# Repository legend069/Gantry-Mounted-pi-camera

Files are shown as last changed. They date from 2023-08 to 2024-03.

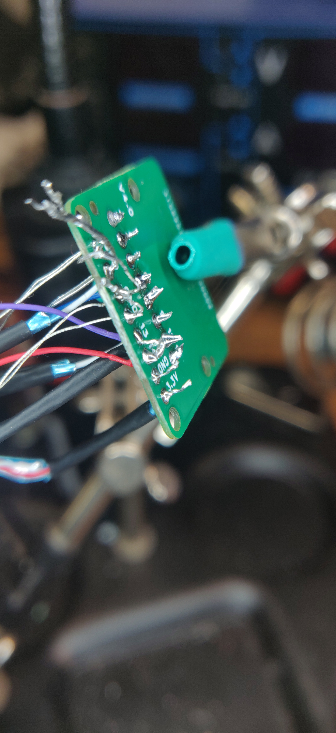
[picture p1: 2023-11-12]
Pictures/Build Process Pictures/IMG_20230614_181707.jpg

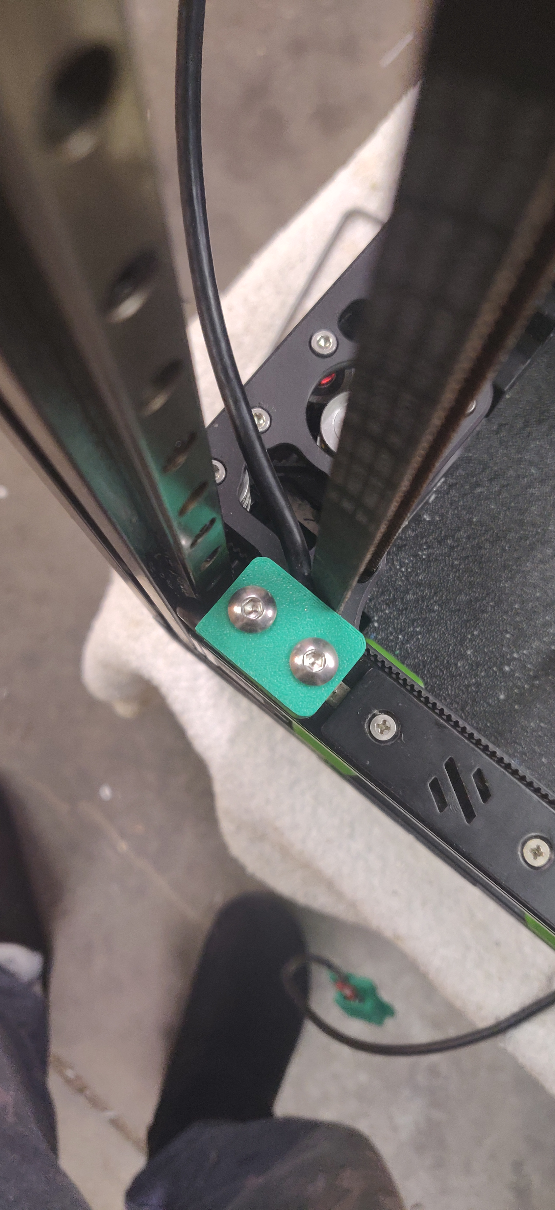
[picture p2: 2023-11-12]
Pictures/Build Process Pictures/IMG_20230511_184907.jpg

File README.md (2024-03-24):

# Gantry-Mounted-pi-camera
description - work in progress  

GPU-Z_GeZQuU00W8

# summary
there are two pi camera versions to choose from.
plug and play - exactly as it sounds. plug cable into PCB's and the FPC cables in and away you go!
  but this one costs more $$ in parts.

raw dog - i like to call it raw dog because you're basically raw dogging it.
  this one is for the soldering experts(or atleast above beginner) you cut up a DP cable(any length as long as it will reach point a to point b)
  strip the very tiny and fragile wires and solder them directly to the PCB.
  is a cheaper for parts. [tips](https://github.com/legend069/Gantry-Mounted-pi-camera/edit/main/README.md#tips-for-soldering-raw-dog)

  note: to help with raw-dog method, i've created a extra [PCB](https://github.com/legend069/Gantry-Mounted-pi-camera/tree/main/gerbers/ready%20to%20order%20files/raw_dog_full_display_port) using this PCB and the normal raw-dog one you only have to cut 1 end of the cable. but since the display port wires get switched inside the cable, you need to figure what end is what before you cut it.

i originally wanted this to be cheap, so i started off with cat5e networking cable. yes this does actually work but only over short distances.<1.5 meter

## whats the differences between the two?
*  plug-play takes up more Z height(this is mainly because of the cable)
*  raw-dog much more compact, but requires a skilled and patient soldering

  the max FPS you can get between the two is the same, the limiter is the camera, my target for the project was 30fps. during my testing phase it can push up to 45(pi camera v3 wide) before it starts to have frame stutter/visable noise.
  if you're going with the raw-dog method getting maxfps (40+) gets harder and harder with the soldering work. because you need to get all 8 wires to the PCB the **same length!**

## tips for soldering raw-dog
* this takes a long time, it'll take around 2 hours to solder both PCB's + add some more time if some wires break :angry: during the trials i broke around 10 wires during moving from the solder work bench to the printer.
* the pro tip i found that helped out a bunch was to use some cat5e(any solid core network cable) and extend the ends of the DisplayPort cable. and heatshrink the bits in between.[picture](https://github.com/legend069/Gantry-Mounted-pi-camera/blob/main/Pictures/Build%20Process%20Pictures/IMG_20230618_065408.png)
* as long as you **cut** the lengths as good as you can, then tin the wires and start soldering. use very light solder with the tinning and PCB work.
  because you can use tweezers and slightly pull/press on the wire to help get it aligned up with the other **this is a critical step!** [reference](https://github.com/legend069/Gantry-Mounted-pi-camera/blob/main/Pictures/Build%20Process%20Pictures/IMG_20230614_181707.jpg) the important wires that need to length match are the top 8 (pads 2-12) the others don't matter. and yes you do need to **solder all the shielded wires to GND** too.
* if you can't get the wires length matching as close as possible to perfect. don't worry, it's not the end of the world. you'll just get frame [stutter/visual noise](https://www.google.com.au/search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) on high framerates.

if you want more pictures they're [here](https://github.com/legend069/Gantry-Mounted-pi-camera/tree/main/Pictures)

the picture below is the raw-dog camera in action- pi camera V3 wide
snapshot

the picture below is the raw-dog camera in action- pi camera V2
snapshotV2cam

and this one is the micro-hdmi (plug and play) pi camera V2
micro1

i don't have the photo for the micro-hdmi (plug and play) pi camera V3 wide(since i didn't have the v3 camera at the time) 

# BOM (build of materials) 
below links is what i bought and are guarenteed to work. you're more than welcome to find others but they might not work.
* for rawdog  
  [FPC cable 50mm](https://au.mouser.com/ProductDetail/710-686715050001)  
  [raw-dog DP-DP cable 2m](https://cplonline.com.au/alogic-eldp-02-elements-2m-displayport-cable-ver-1-2-male-to-male.html) - PN alogic ELDP-02  
  M2 screws 12mm x4 & 16mm x4  

* plug and play(micro-hdmi)  
  [FPC cable 50mm](https://au.mouser.com/ProductDetail/710-686715050001)  
  [micro-hdmi to hdmi cable 2m](https://www.digikey.com.au/en/products/detail/tripp-lite/P570-006-MICRO/4438902)  
  [adapter](https://www.digikey.com.au/en/products/detail/seeed-technology-co-ltd/320210001/5487747)  
  M2 screws 12mm-14mm x4 & 20mm x4   

### alternates
[adapter alternate-UN TESTED](https://au.mouser.com/ProductDetail/Seeed-Studio/320210001?qs=SElPoaY2y5IpesjEUALrcQ%3D%3D)  
[cheaper option-UN TESTED](https://au.rs-online.com/web/p/raspberry-pi-cables/1871376)  
[FPC cable 50mm alternate](https://www.digikey.com.au/short/bmt4hz0f)  

# FAQ
* can i destroy my pi camera using this?  
  no, not unless you mess up the wiring with raw-dog method.
* do i have to use your repo?  
  no, you're more than welcome to use any other pi camera streaming software.
* do i need supports for the printable files?  
  for most of them yes, but use your 3d printing knowledge to determine if some areas are needed or not.
* will the cable that's inside the y extrusion wear out over time?  
  no, the cable i spefically looked for would fit nicely in the gaps and not have any clearance issues.
* do i need a second drag chain for this?  
  only if your current drag chain won't be able to fit the extra cable.
* will i lose any printable height in XYZ?  
  no, not for the raw-dog camera
  for the micro-hdmi version you shouldn't but then you have a different printer to me, so check the cad file 😄
* how much networking bandwidth does this use?  
  for the V3 camera -camera-width=2304 -camera-height=1296 at 30 fps it's around 50mbps while watching the stream.
  if you close the stream from your phone/pc tab the stream will end and stop using the network bandwidth.
* can i use this for timelapes?  
  you sure can! it's still your standard pi camera.

# sounds great! how i get one?
  order the parts from digikey/mouser
  [gerber files](https://github.com/legend069/Gantry-Mounted-pi-camera/tree/main/gerbers/ready%20to%20order%20files)
  steps for PCB ordering coming soon....

```diff
- note:PCB thickness must be 0.8mm!
```

## repo download
```
cd ~
git clone https://github.com/legend069/Gantry-Mounted-pi-camera.git
```
## install commands
```
sudo apt-get -y install libavformat-dev libavutil-dev libavcodec-dev libcamera-dev liblivemedia-dev v4l-utils pkg-config xxd build-essential
cd ~
ln -s /home/pi/Gantry-Mounted-pi-camera/repo/camera-streamer /home/pi/camera-streamer
cd camera-streamer/
make
sudo make install
```
## setup commands for camera
```
systemctl enable $PWD/service/camera-streamer-raspi-v2-8MP.service 
systemctl start camera-streamer-raspi-v2-8MP 
------or------ 
systemctl enable $PWD/service/camera-streamer-raspi-v3-12MP.service 
systemctl start camera-streamer-raspi-v3-12MP.service 
```
### to view logs
``journalctl -xef -u camera-streamer-raspi-v2-8MP ``

all the credit for the code goes to this guy https://github.com/ayufan/camera-streamer

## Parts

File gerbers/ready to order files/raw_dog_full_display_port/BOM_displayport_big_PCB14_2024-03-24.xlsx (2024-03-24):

No. | Quantity | Comment | Designator | Footprint | Value | Manufacturer Part | Manufacturer | Supplier Part | Supplier
1 | 1 | 3VD51203-3D6A-7H | CN2 | DP-SMD_3VD51203-3D6A-7H |  | 3VD51203-3D6A-7H | FOXCONN(富士康) | C2761456 | LCSC
2 | 1 | F1003WR-S-15PNLNG1GB0R | FPC2 | FPC-SMD_15P-P1.00_L5.5-W22.0 |  | F1003WR-S-15PNLNG1GB0R | HR(灿达) | C247796 | LCSC

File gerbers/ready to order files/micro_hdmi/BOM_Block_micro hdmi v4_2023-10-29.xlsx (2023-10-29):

No. | Quantity | Comment | Designator | Footprint | Value | Manufacturer Part | Manufacturer | Supplier Part | Supplier
1 | 1 | F1003WR-S-15PNLNG1GB0R | FPC1 | FPC-SMD_15P-P1.00_L5.5-W22.0 |  | F1003WR-S-15PNLNG1GB0R | HR(灿达) | C247796 | LCSC
2 | 1 | HDMI-101S | USB1 | HDMI-SMD_HDMI-101S |  | HDMI-101S | XUNPU(讯普) | C720620 | LCSC

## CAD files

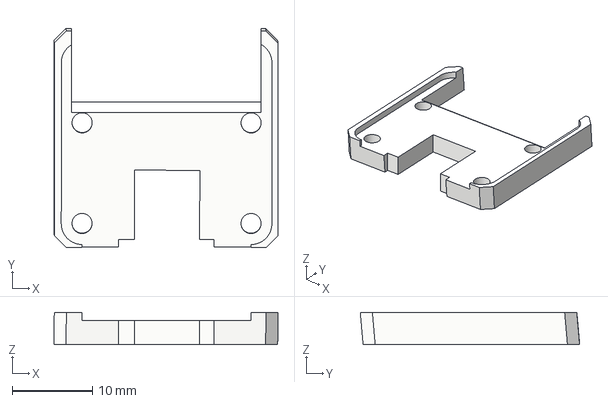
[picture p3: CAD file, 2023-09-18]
3mf printable files/micro-hdmi/first-prototype-mounting/microHDMI_mid2.3mf
27.8 x 27.3 x 4.00 mm

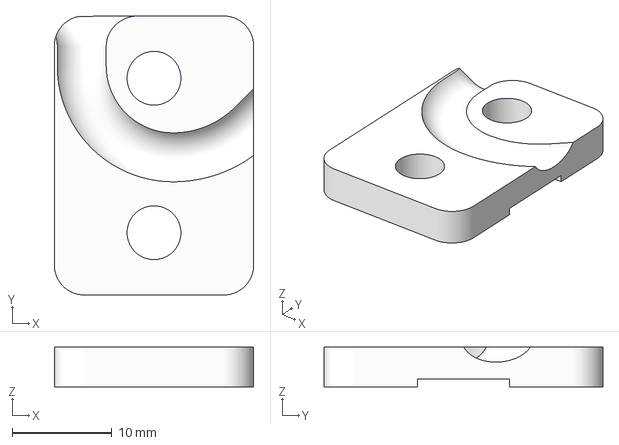
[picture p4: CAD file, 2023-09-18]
3mf printable files/motor-side-parts/motor_end_1.3mf
20.0 x 28.0 x 4.00 mm

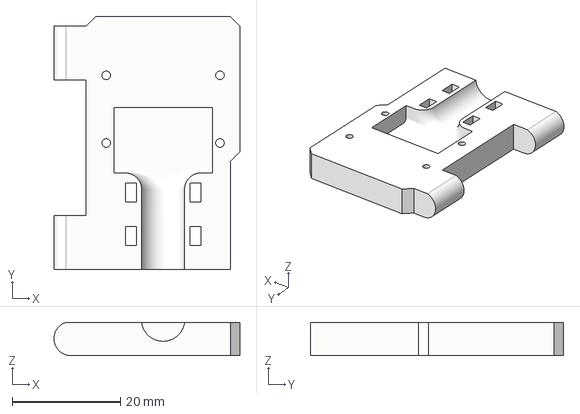
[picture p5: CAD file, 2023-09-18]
3mf printable files/pi-side-parts/RawDog_pi_end_2.3mf
34.3 x 46.8 x 6.15 mm

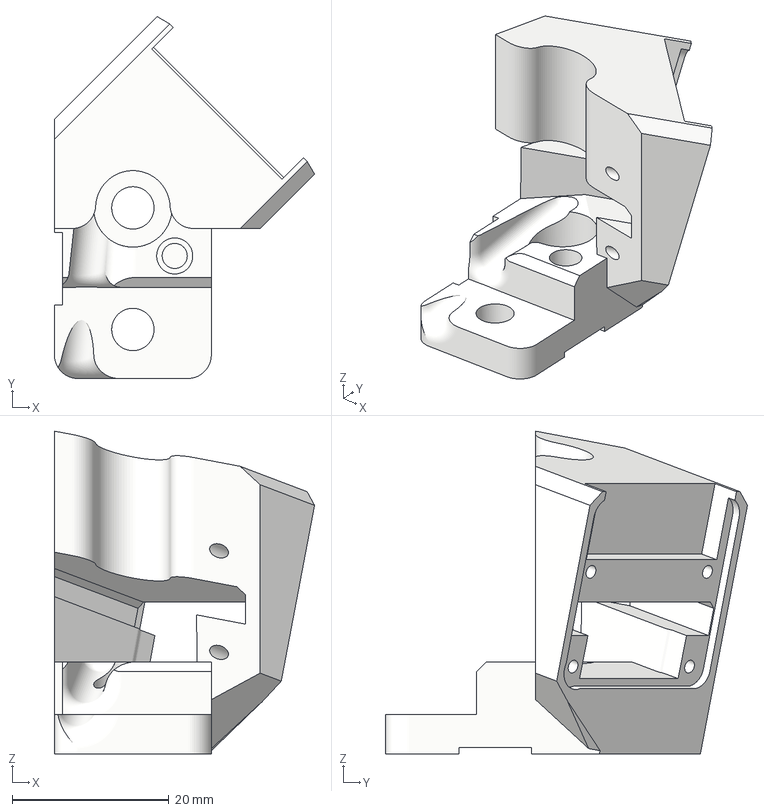
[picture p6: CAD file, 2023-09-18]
3mf printable files/raw-dogV2camera/first-prototype-mounting/RawDog_bottom_V3.3mf
33.2 x 46.1 x 41.1 mm

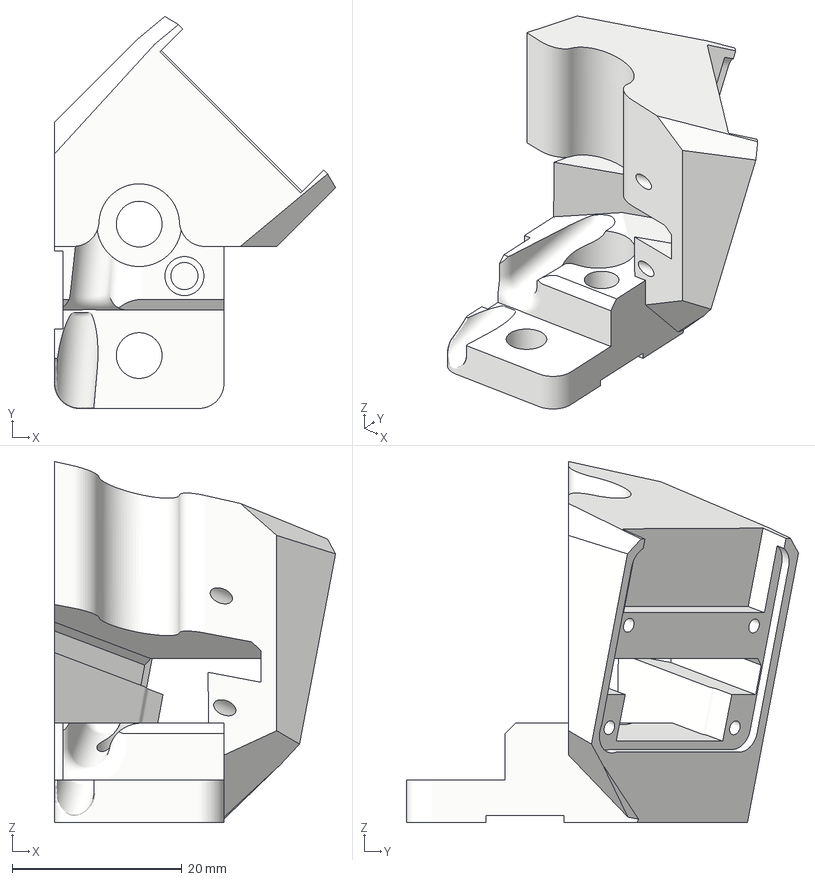
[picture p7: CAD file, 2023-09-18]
3mf printable files/raw-dogV3camera/first-prototype-mounting/RawDog_bottom_V3 (1).3mf
33.2 x 46.2 x 42.6 mm

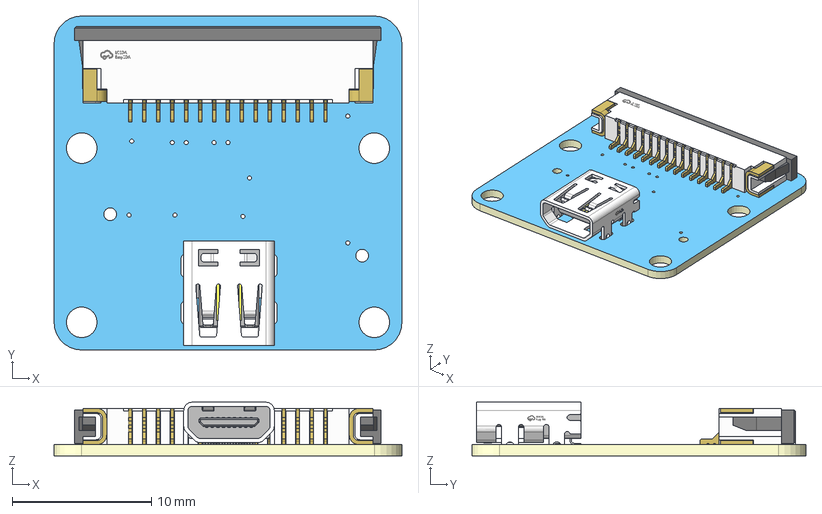
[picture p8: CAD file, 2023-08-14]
CAD files/PCB-MicroHDMI/micro hdmi PCB v1.step
25.0 x 24.0 x 3.85 mm

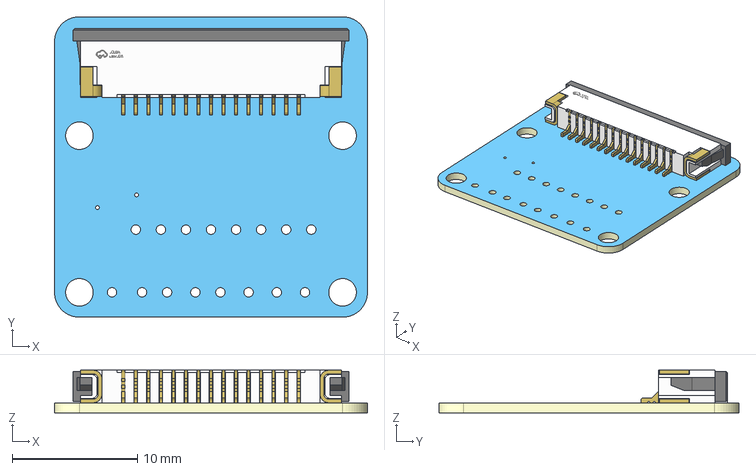
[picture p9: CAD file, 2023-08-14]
CAD files/PCB-RawDog/RawDog PCB v2.step
25.0 x 24.0 x 3.40 mm

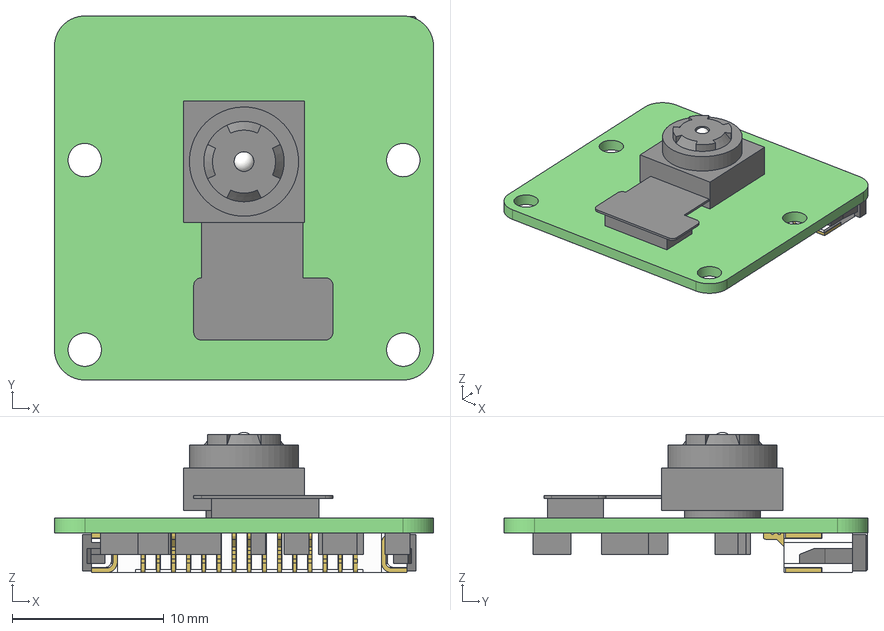
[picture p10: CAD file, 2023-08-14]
CAD files/pi Camera V2/RPi Camera V2.1 v12.step
25.0 x 24.0 x 9.25 mm
PCB
Zif Connector
Camera Lense
Camera PCB connector

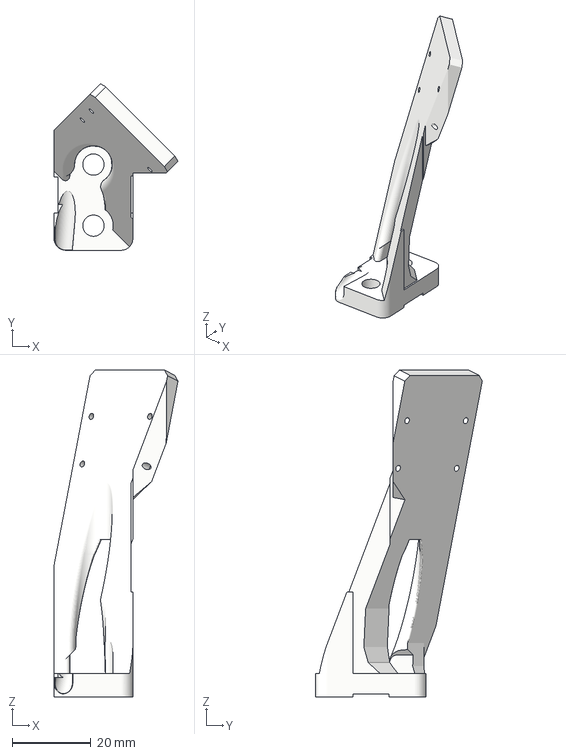
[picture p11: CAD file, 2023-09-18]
3mf printable files/micro-hdmi/first-prototype-mounting/microHDMI_bottomV4.3mf
31.4 x 42.2 x 82.9 mm

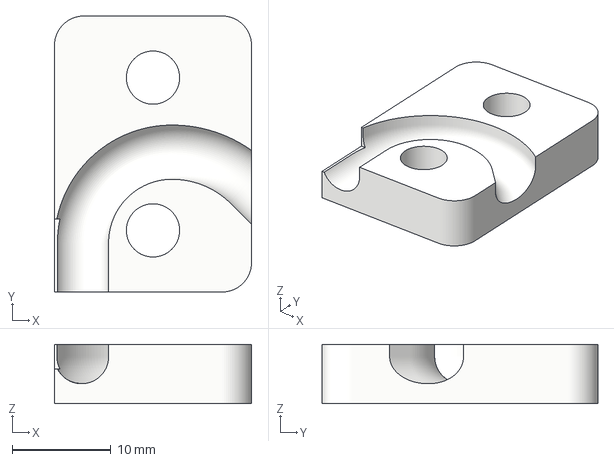
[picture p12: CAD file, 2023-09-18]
3mf printable files/motor-side-parts/motor_end_2.3mf
20.0 x 28.0 x 6.00 mm

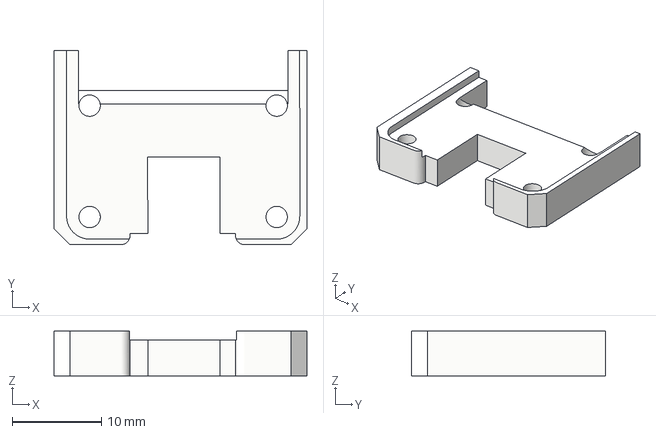
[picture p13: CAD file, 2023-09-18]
3mf printable files/pi-side-parts/microHDMI_pi_end_1.3mf
28.4 x 21.8 x 5.00 mm

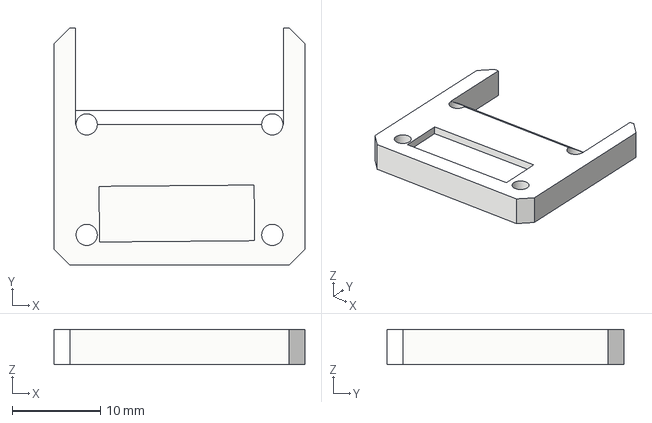
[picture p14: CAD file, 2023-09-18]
3mf printable files/raw-dogV2camera/first-prototype-mounting/RawDog_mid.3mf
28.4 x 26.8 x 4.00 mm

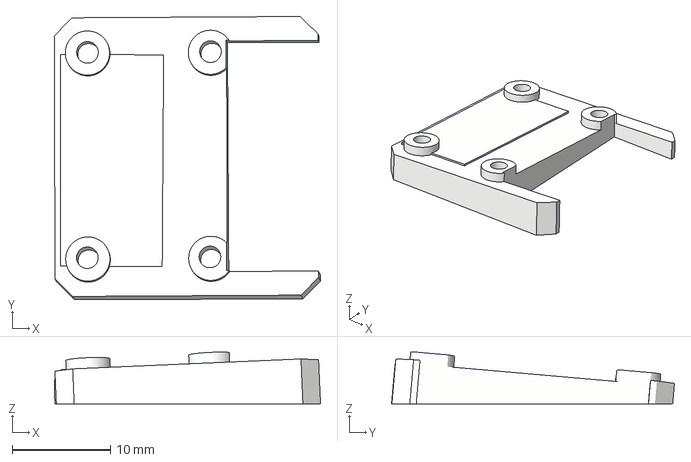
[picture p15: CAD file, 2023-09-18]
3mf printable files/raw-dogV3camera/first-prototype-mounting/RawDog_midV3.3mf
27.0 x 28.7 x 5.26 mm

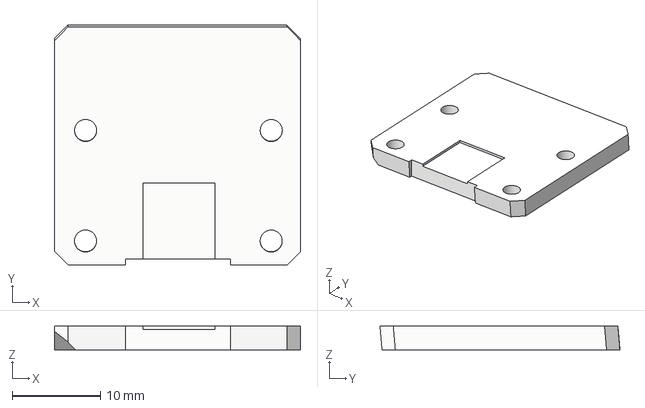
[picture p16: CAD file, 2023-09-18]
3mf printable files/micro-hdmi/first-prototype-mounting/microHDMI_mid3.3mf
27.8 x 27.2 x 2.67 mm

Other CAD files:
3mf printable files/motor-side-parts/motor_end_3.3mf
3mf printable files/pi-side-parts/microHDMI_pi_end_3.3mf
3mf printable files/raw-dogV2camera/first-prototype-mounting/RawDog_top.3mf
3mf printable files/raw-dogV3camera/first-prototype-mounting/RawDog_top-V3cam.3mf
3mf printable files/micro-hdmi/first-prototype-mounting/microHDMI_mid1.3mf
3mf printable files/micro-hdmi/first-prototype-mounting/microHDMI_top.3mf
3mf printable files/pi-side-parts/RawDog_pi_end_1.3mf
3mf printable files/pi-side-parts/RawDog_pi_end_3.3mf
3mf printable files/pi-side-parts/microHDMI_pi_end_2.3mf
CAD files/PCB-MicroHDMI/micro hdmi PCB v1.f3d
CAD files/PCB-RawDog/RawDog PCB v2.f3d
CAD files/full assembly files/RawDog Camera v3.f3z
CAD files/full assembly files/temp gantry mounted pi camera v1.f3d
CAD files/pi Camera V2/RPi Camera V2.1 v12.f3d

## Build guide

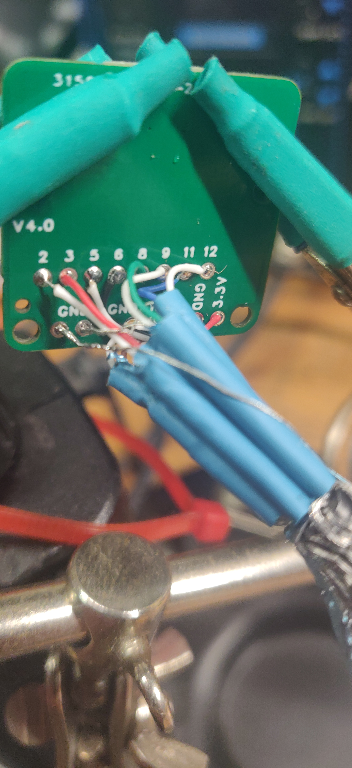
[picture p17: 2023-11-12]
Pictures/Build Process Pictures/IMG_20230511_234410.jpg

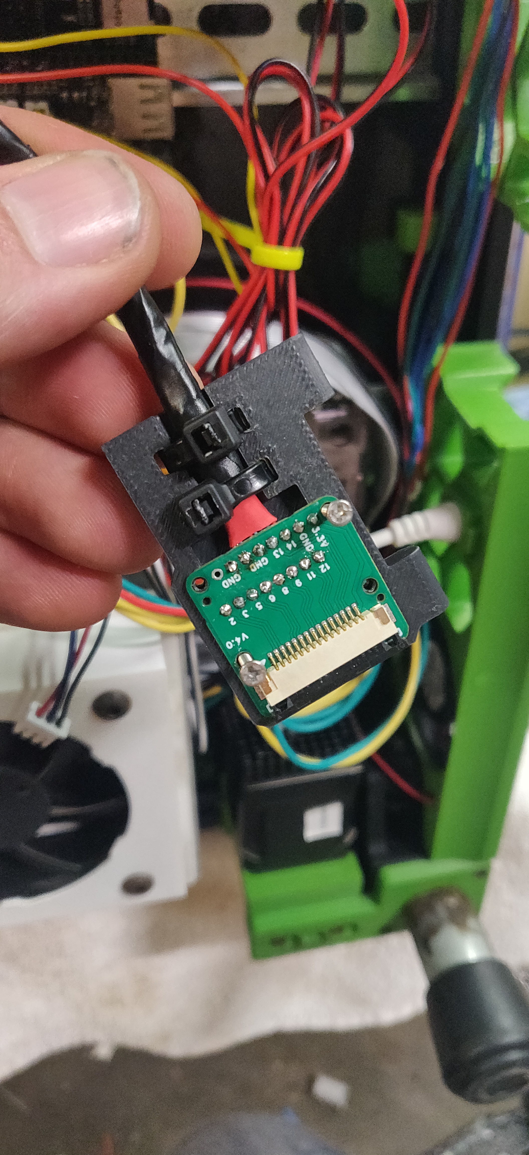
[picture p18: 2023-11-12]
Pictures/Build Process Pictures/IMG_20230910_193127.jpg

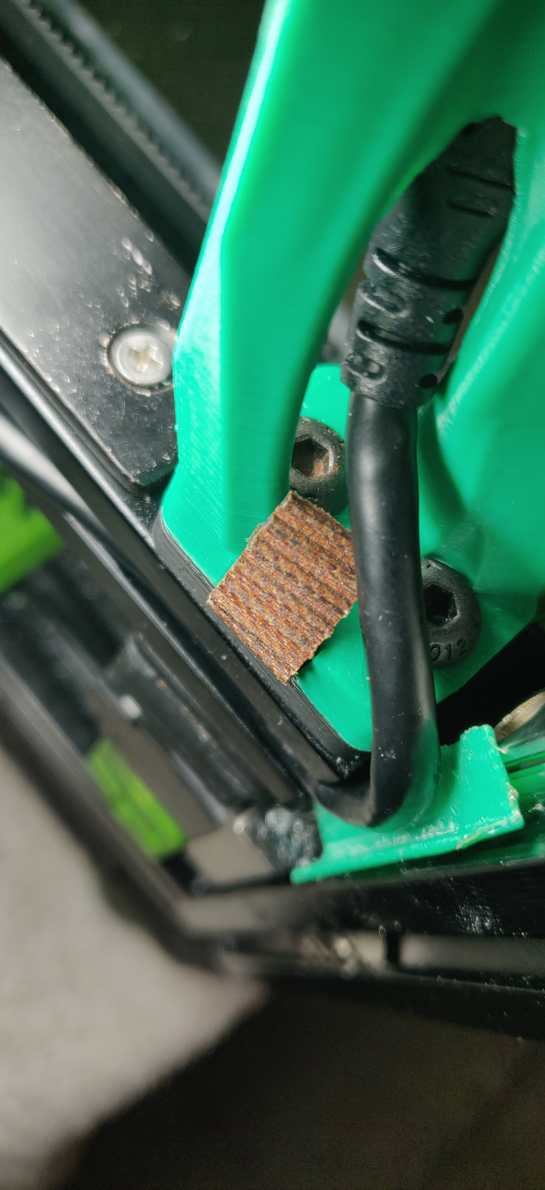
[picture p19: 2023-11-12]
Pictures/Build Process Pictures/IMG_20230520_174456.jpg

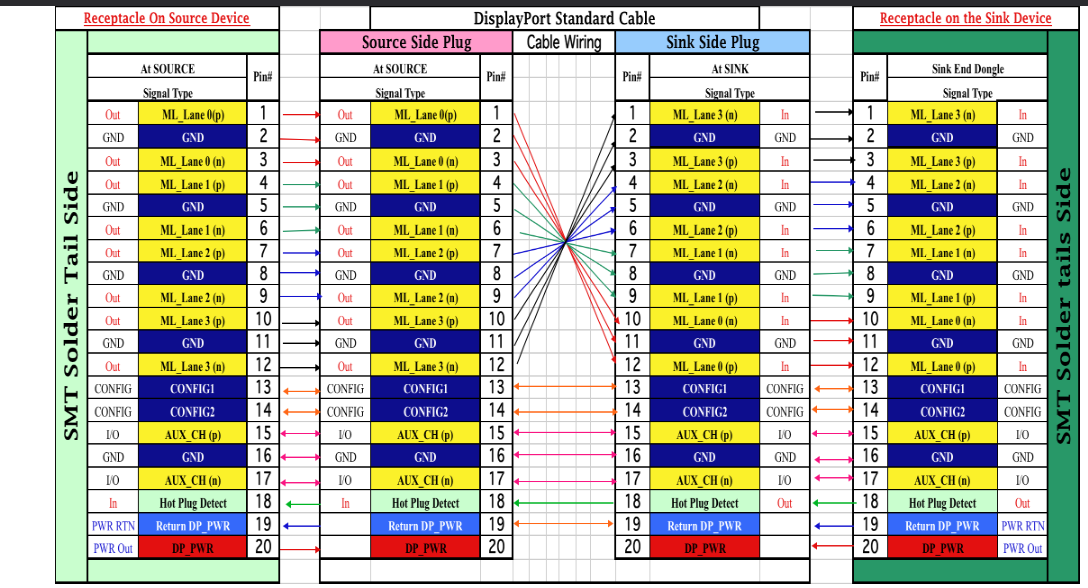
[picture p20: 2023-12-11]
Pictures/cable wiring pictures/firefox_FRXW8FDyAQ.png

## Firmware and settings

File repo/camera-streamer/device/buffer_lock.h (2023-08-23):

#pragma once

#include <stdbool.h>
#include <stdint.h>
#include <pthread.h>

typedef struct buffer_s buffer_t;
typedef struct buffer_list_s buffer_list_t;
typedef struct buffer_lock_s buffer_lock_t;

typedef bool (*buffer_lock_check_streaming)(buffer_lock_t *buf_lock);
typedef void (*buffer_lock_notify_buffer)(buffer_lock_t *buf_lock, buffer_t *buf);

#define BUFFER_LOCK_MAX_CALLBACKS 10

typedef struct buffer_lock_s {
  const char *name;
  buffer_list_t *buf_list;

  buffer_lock_check_streaming check_streaming[BUFFER_LOCK_MAX_CALLBACKS];
  buffer_lock_notify_buffer notify_buffer[BUFFER_LOCK_MAX_CALLBACKS];

  // private
  pthread_mutex_t lock;
  pthread_cond_t cond_wait;
  buffer_t *buf;
  uint64_t buf_time_us;
  int counter;
  int refs;
  int dropped;
  uint64_t timeout_us;

  int frame_interval_ms;
} buffer_lock_t;

#define DEFAULT_BUFFER_LOCK_TIMEOUT 16 // ~60fps
#define DEFAULT_BUFFER_LOCK_GET_TIMEOUT 2000 // 2s

#define DEFINE_BUFFER_LOCK(_name, _timeout_ms) buffer_lock_t _name = { \
    .name = #_name, \
    .lock = PTHREAD_MUTEX_INITIALIZER, \
    .cond_wait = PTHREAD_COND_INITIALIZER, \
    .timeout_us = (_timeout_ms > DEFAULT_BUFFER_LOCK_TIMEOUT ? _timeout_ms : DEFAULT_BUFFER_LOCK_TIMEOUT) * 1000LL, \
  };

#define DECLARE_BUFFER_LOCK(_name) extern buffer_lock_t _name;

typedef int (*buffer_write_fn)(buffer_lock_t *buf_lock, buffer_t *buf, int frame, void *data);

void buffer_lock_capture(buffer_lock_t *buf_lock, buffer_t *buf);
buffer_t *buffer_lock_get(buffer_lock_t *buf_lock, int timeout_ms, int *counter);
bool buffer_lock_needs_buffer(buffer_lock_t *buf_lock);
void buffer_lock_use(buffer_lock_t *buf_lock, int ref);
bool buffer_lock_is_used(buffer_lock_t *buf_lock);
int buffer_lock_write_loop(buffer_lock_t *buf_lock, int nframes, unsigned timeout_ms, buffer_write_fn fn, void *data);
bool buffer_lock_register_check_streaming(buffer_lock_t *buf_lock, buffer_lock_check_streaming check_streaming);
bool buffer_lock_register_notify_buffer(buffer_lock_t *buf_lock, buffer_lock_notify_buffer notify_buffer);

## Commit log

2023-08-14 pictures and cad files
    [RPi Camera V2.1 v12.f3d, RPi Camera V2.1 v12.step, RawDog Camera v3.f3z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]
2023-08-14 couple more pictures/mp4
2023-09-18 added files for 3mf printing aligned
    added files aligned to origin in fusion360
    tested and no werid artifacts on top layers.
    [RawDog_bottom_V3 (1).3mf, RawDog_bottom_V3.3mf, RawDog_mid.3mf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]
2023-10-10 printed parts list
    required printed parts for each version
2023-10-29 gerber files upload
    uploaded gerber files and project files. fixed pi cam v3 service file for project default values.
    [BOM_Block_PCB_pi camera_v4_2023-10-29.xlsx, BOM_Block_micro hdmi v4_2023-10-29.xlsx, PickAndPlace_PCB_pi camera_v4_2023-10-29.xlsx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]
2024-03-24 new displayport PCB added
    using the full displayport PCB saves you having to cut both ends of a cable.
    but since the DP cable is swaps the wires around inside the cable you need to figure out what end is correct before cutting it.
    [BOM_displayport_big_PCB14_2024-03-24.xlsx, PickAndPlace_PCB14_2024-03-24.xlsx]
2024-03-24 Update README.md
    added details for full display port PCB
